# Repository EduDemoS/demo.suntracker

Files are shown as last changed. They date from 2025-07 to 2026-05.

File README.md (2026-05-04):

# EduDemoS Sun-Tracker

This "Sun-Tracker" is our most advanced demonstrator. Similar to a real sunflower, it turns its flower towards the sun to collect as much light as possible. Like the Modular Weather Station, it can send data to the Internet via MQTT. For your convenience there are two sets of instructions. One includes step-by-step instructions for building the complete Sun-Tracker. The other is an abbreviated version suitable for a four-hour workshop and assumes that all soldering and other preparatory work has already been completed.

This repository contains all necessary files and is structured as follows:

- [doc](doc) contains documentation such as
  - assembly manual
  - bill of material
- [code](code) contains program code to run the model
  - [Sun-Tracker preparation firmware](code/Sun-Tracker_Preparation)
  - [Sun-Tracker offline](code/Sun-Tracker)
  - [Sun-Tracker 🌐 IoT ready](code/sun_tracker_iot)
- [dashboards](dashboards) contains example dashboards for ThingsBoard (see [description below](#using-the-example-dashboards)).
- [model](model) contains the printable 3D model

## Using the example dashboards

The example dashboards are tailored for the [IoT variant of the control software](code/sun_tracker_iot/)
To use the example dashboards:

1. Import the JSON file as ThingsBoard dashboard
2. Enter edit mode
3. For each widget adjust:
   - if the target device field is empty: Enter the appropriate target device.
   - if the target device field is not empty, the dashboard features an [entity alias](https://thingsboard.io/docs/user-guide/ui/aliases/#single-entity) to reference the target device. In this case [edit the alias](https://thingsboard.io/docs/user-guide/ui/aliases/#creating-alias) to have it pointing towards the appropriate target device.
4. Save the dashboard

## Licensing

Please note: different licenses apply depending on the type of content.

All documents and 3d models (files ending with .pdf and .stl) are licensed under [CC-BY-NC-SA 4.0](https://creativecommons.org/licenses/by-nc-sa/4.0/).

All files containing code are licensed under [GNU GPL V3](https://www.gnu.org/licenses/gpl-3.0.txt).

## Disclaimer:

Funded by the European Union. Views and opinions expressed are however those of the author(s) only and do not necessarily reflect those of the European Union or the European Education and Culture Executive Agency (EACEA). Neither the European Union nor EACEA can be held responsible for them.

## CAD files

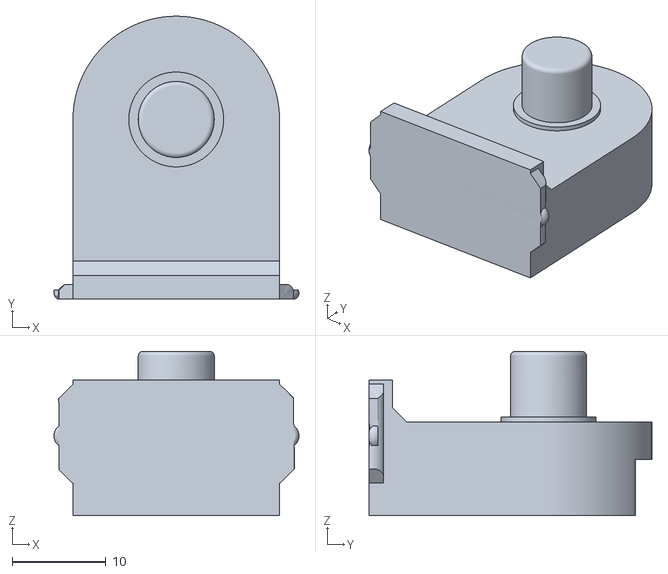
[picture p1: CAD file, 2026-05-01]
model/Flowerhead Joint R.stl
26.1 x 30.1 x 17.5

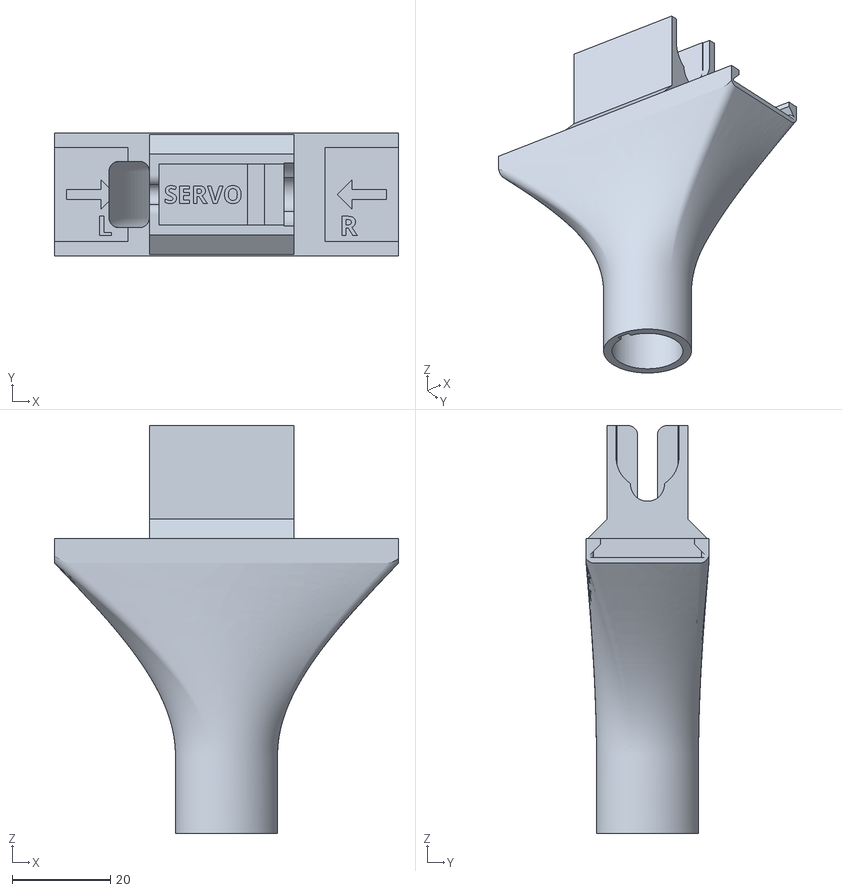
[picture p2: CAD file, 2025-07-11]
model/Stem Top Segment.stl
70.0 x 25.0 x 83.0

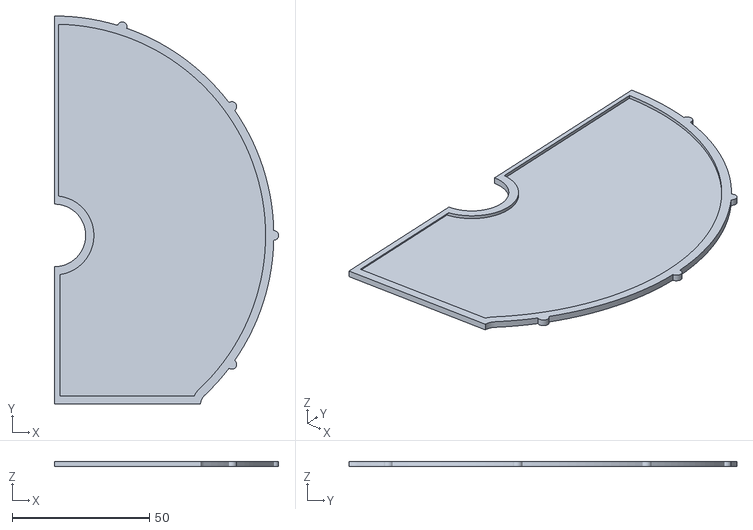
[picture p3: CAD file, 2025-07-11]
model/Pot Cover L.stl
81.7 x 141.5 x 2.00

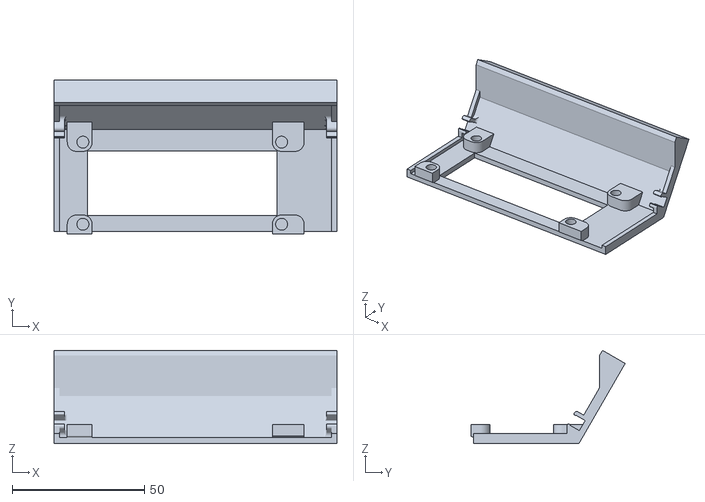
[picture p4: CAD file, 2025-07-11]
model/LCD Frame.stl
106.8 x 58.3 x 35.2

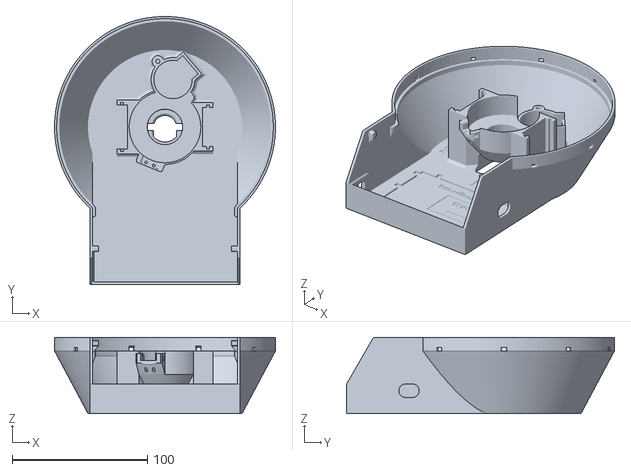
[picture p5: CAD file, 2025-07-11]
model/Flowerpot.stl
163.6 x 198.4 x 56.5

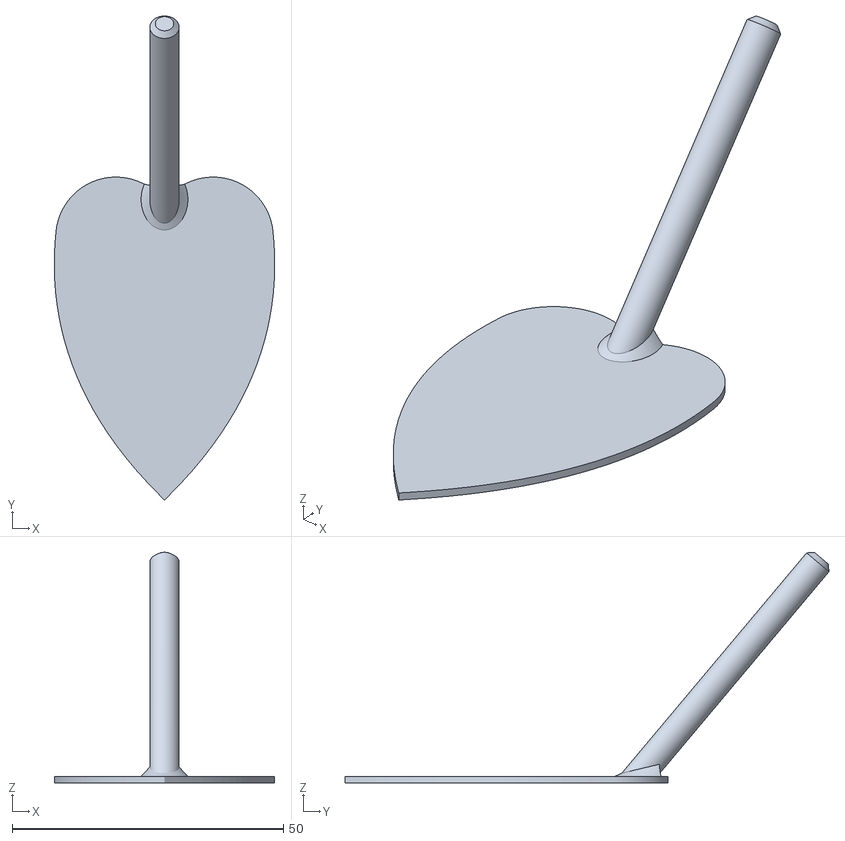
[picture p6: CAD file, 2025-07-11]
model/Stem Leaf.stl
40.6 x 89.3 x 42.5

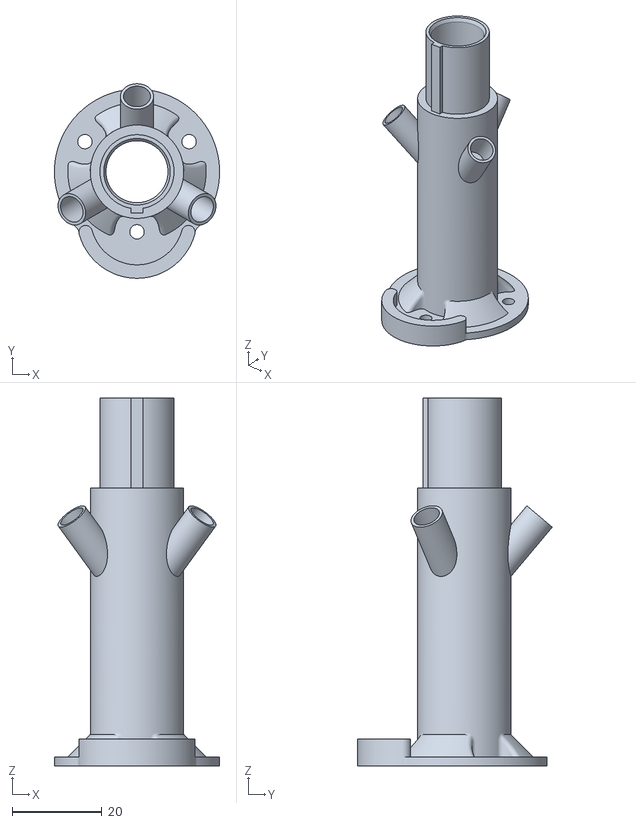
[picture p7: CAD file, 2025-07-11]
model/Stem Leaf Segment.stl
36.8 x 43.4 x 82.0

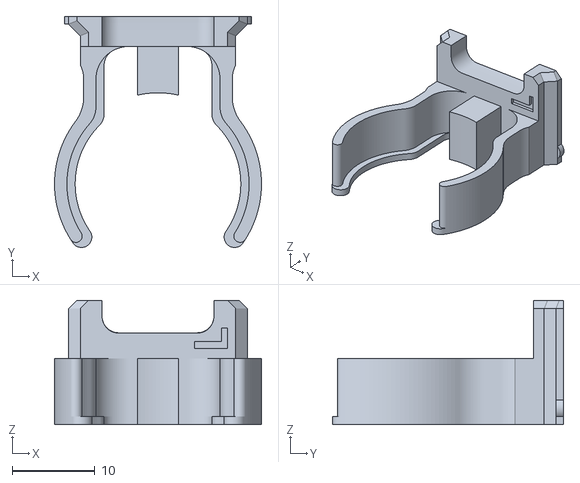
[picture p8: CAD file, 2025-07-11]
model/Flowerhead Clip L.stl
25.0 x 27.9 x 15.0

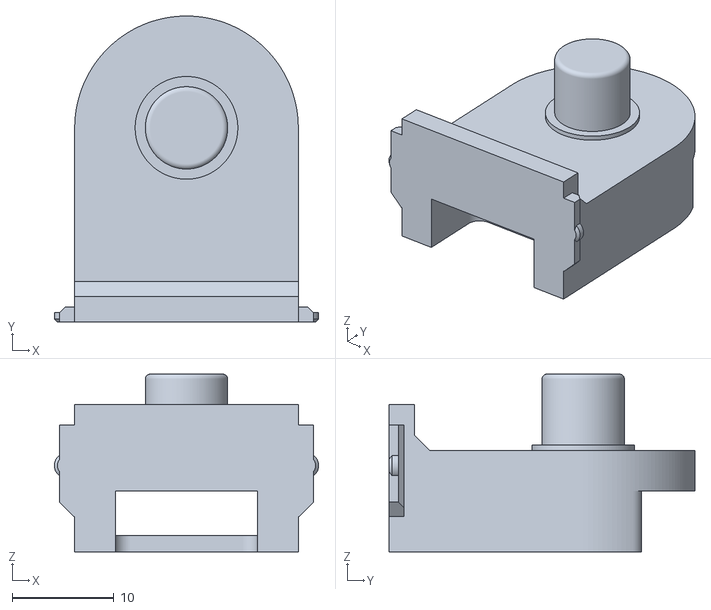
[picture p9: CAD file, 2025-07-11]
model/Flowerhead Joint L.stl
26.0 x 30.1 x 17.5

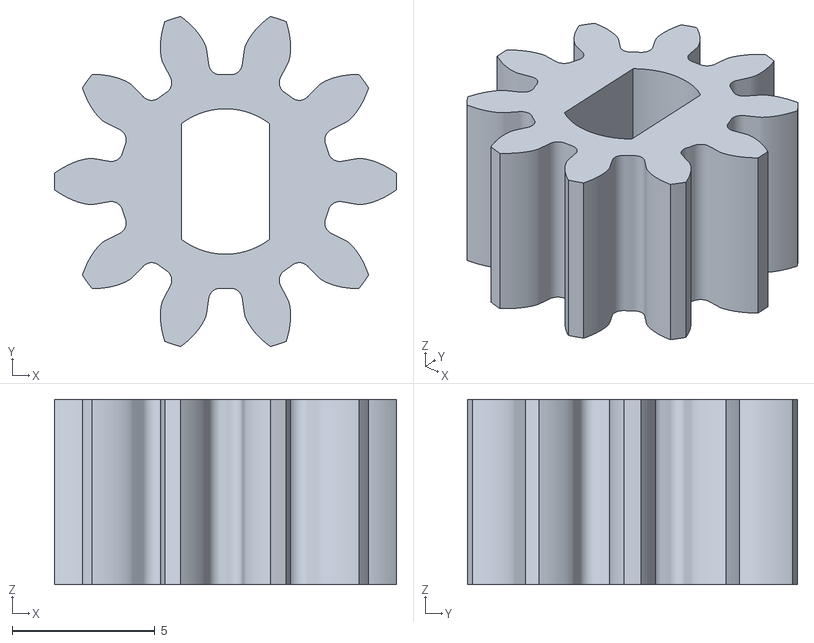
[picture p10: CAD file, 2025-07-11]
model/Motor Gear.stl
12.0 x 11.6 x 6.50

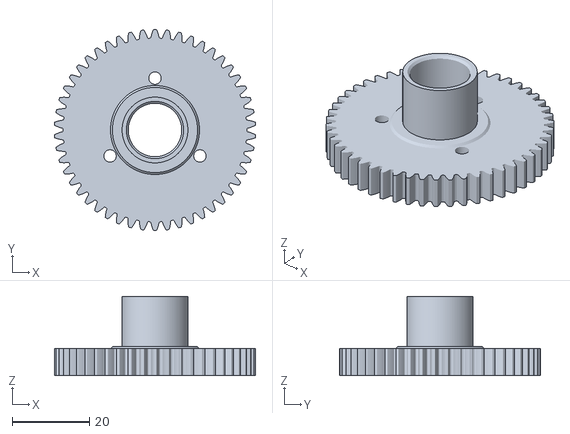
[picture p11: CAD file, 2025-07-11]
model/Large Gear.stl
51.9 x 52.0 x 20.5

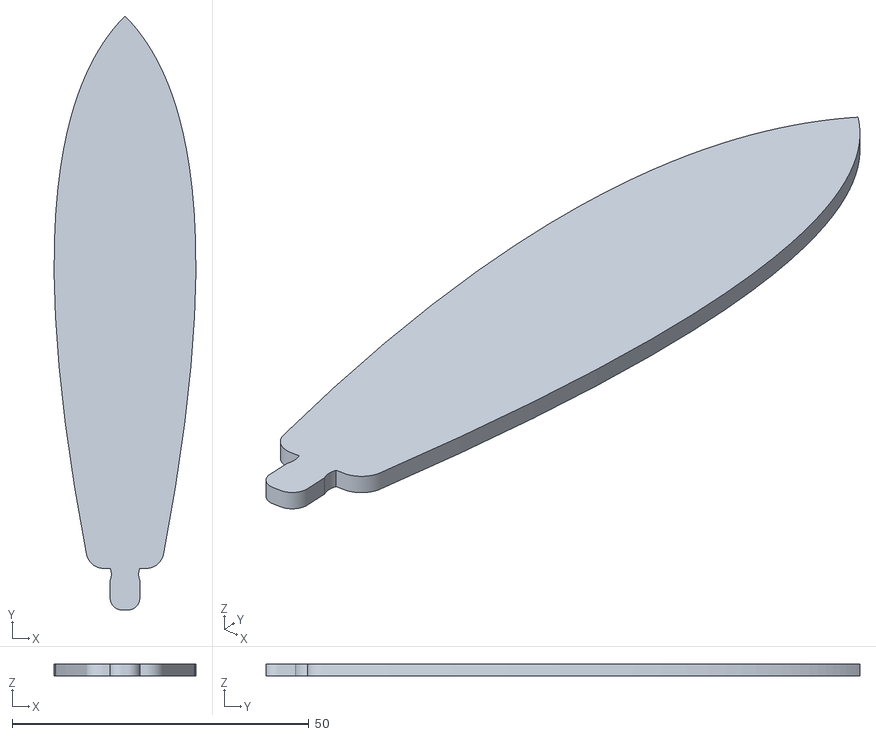
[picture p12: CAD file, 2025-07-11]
model/Flowerhead Leaf.stl
23.9 x 100.0 x 2.00

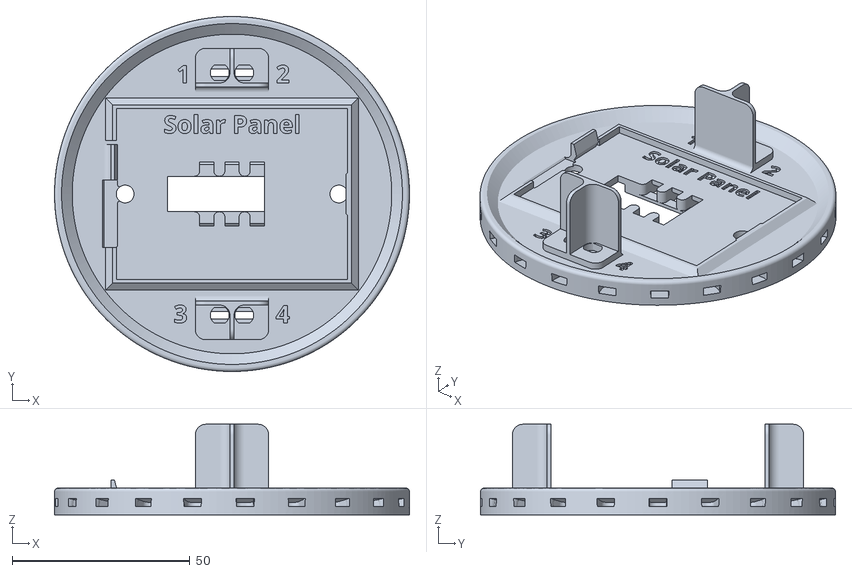
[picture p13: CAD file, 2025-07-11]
model/Flowerhead Base.stl
100.0 x 100.0 x 25.5

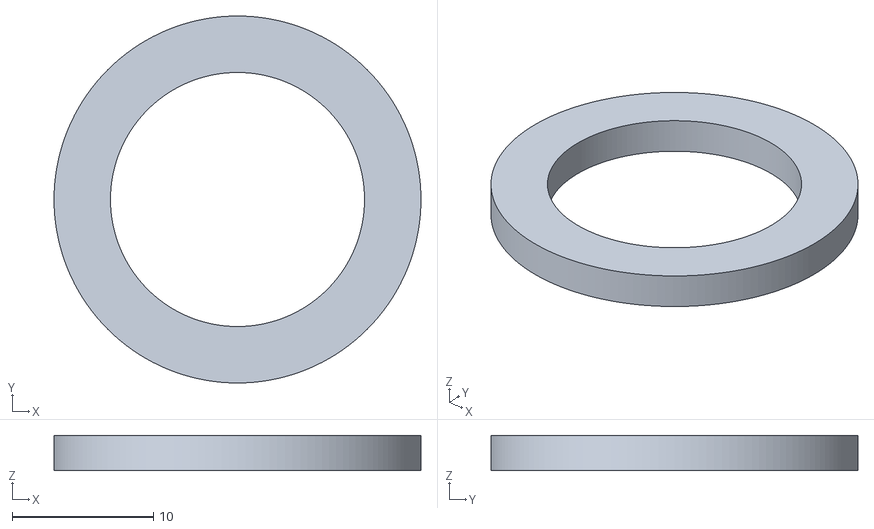
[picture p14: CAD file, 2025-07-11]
model/Bearing Spacer.stl
26.0 x 26.0 x 2.50

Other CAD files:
model/Pot Cover R.stl
model/Stem Segment.stl
model/Flowerhead Clip R.stl

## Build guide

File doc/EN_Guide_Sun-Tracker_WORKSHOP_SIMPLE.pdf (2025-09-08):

# Shortened Workshop Guide Sun-Tracker

# EDUcating through Sustainable DEMOnstrators

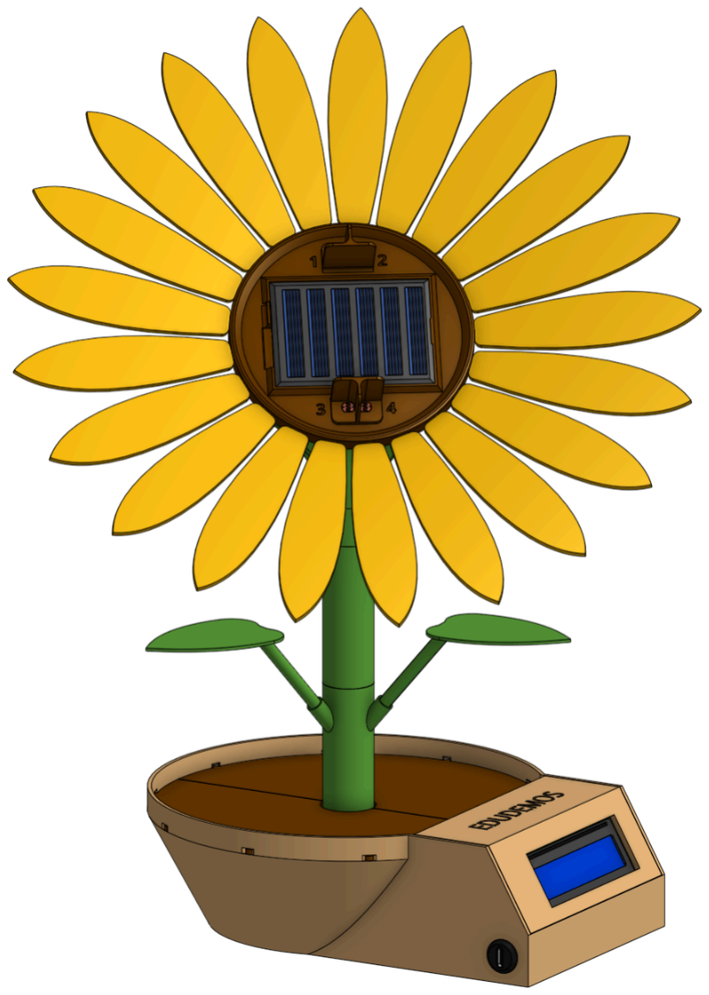
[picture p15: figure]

Funded by the European Union. Views and opinions expressed are however those of the author(s) only and do not necessarily reflect those of the European Union or the European Education and Culture Executive Agency (EACEA). Neither the European Union nor EACEA can be held responsible for them.
V-09.25

# Materials

# Printed Parts

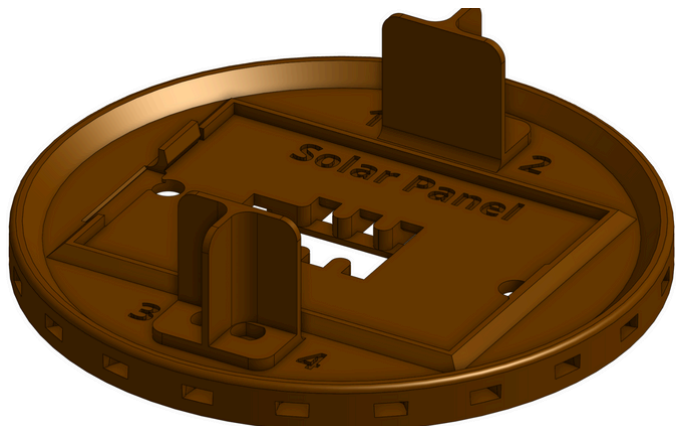
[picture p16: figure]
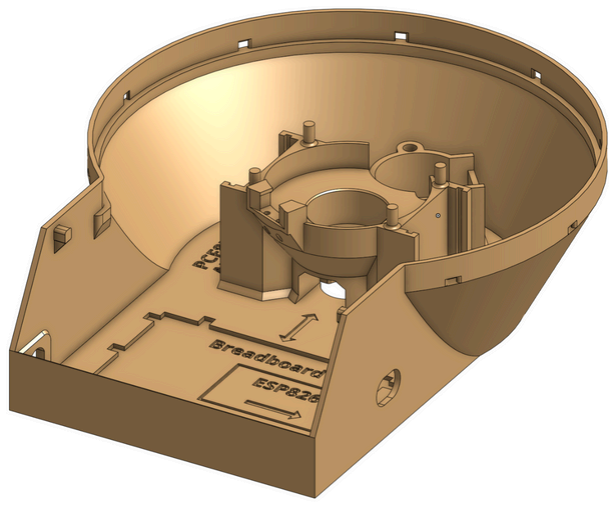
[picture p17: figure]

1x Large Gear | 1x Flowerpot | 1x Motor Gear

1x Stem
Segment

3x Stem Leaf

1x Pot Cover R | 1x Pot Cover L | 1x Stem Top Segment

1x Flowerhead
Clip R

1x Flowerhead
Base

1x Flowerhead
Joint L

1x Flowerhead
Joint R

21x Flowerhead
Leaf

1x Flowerhead
Clip L

1x Leaf
Segment

1x Bearing
Spacer

1x LCD Frame

Print Settings:
All STL-files already have the optimal orientation for printing. Enable supports starting only on the build plate.

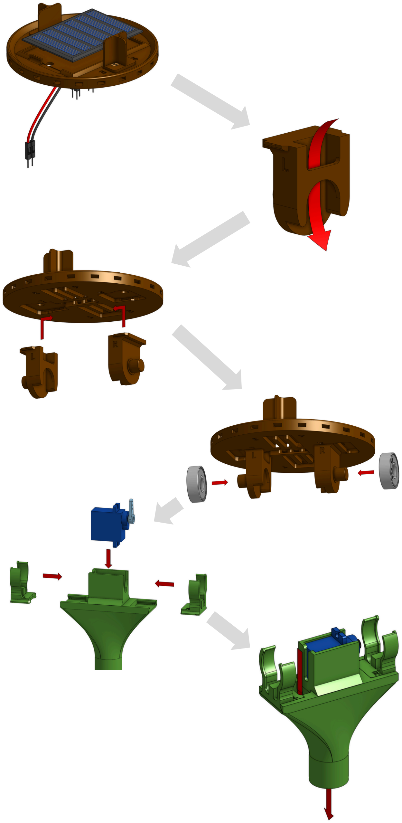
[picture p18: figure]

1.1: Guide the Solar Panel wires from the top through the central hole of the Flowerhead Base and attach it in its frame.

1.2: Then guide all wires (7) coming from the Flowerhead Base through the tunnel in the Flowerhead Joint L.

1.3: Move the Joint L all the way up to the Base and slide it into place.

1.4: Attach Flowerhead Joint R the same way on the opposite side.

1.5: Push the two 608zz Bearings onto the joints.

1.6: Attach both Flowerhead Clips and the Servo Motor in the Stem Top Segment.

1.7: Guide the Servo Motor wires all the way through the hole in the Top Segment.
Do the same with all wires coming from the Flowerhead Assembly.

The wires you have might have different colors than the ones shown here. This is not a problem. Only the connectors are important:
To help you keep track of which wire belongs where, you can note down the actual colors on the “Wire Colors” table.

# 1: Flowerhead Assembly

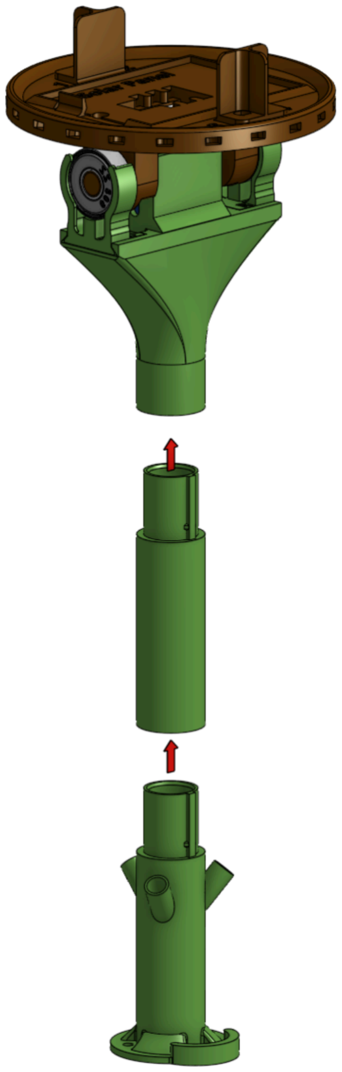
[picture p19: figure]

1.9: Take the Stem Segment, guide the wires through it and attach it to the Top Segment.

1.10: Do the same for the Leaf Segment.

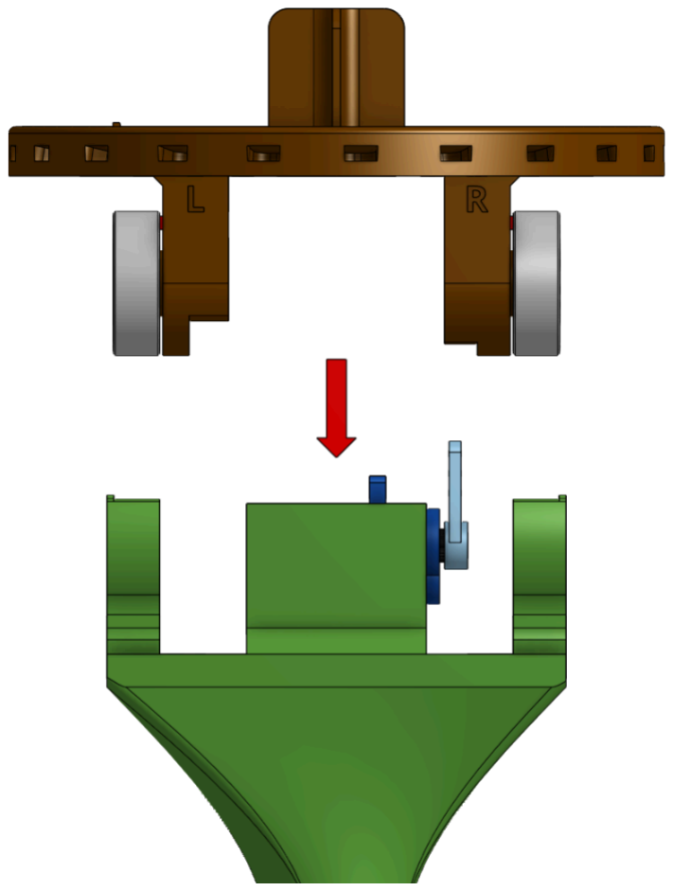
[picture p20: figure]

1.8: Attach the Flowerhead Assembly to the Top Segment by pushing the Bearings into their clips.
Make sure to cleanly pull all the wires through the Top Segment and that they are still grouped together with tape!

# 2: Wiring and Assembly: Flowerpot

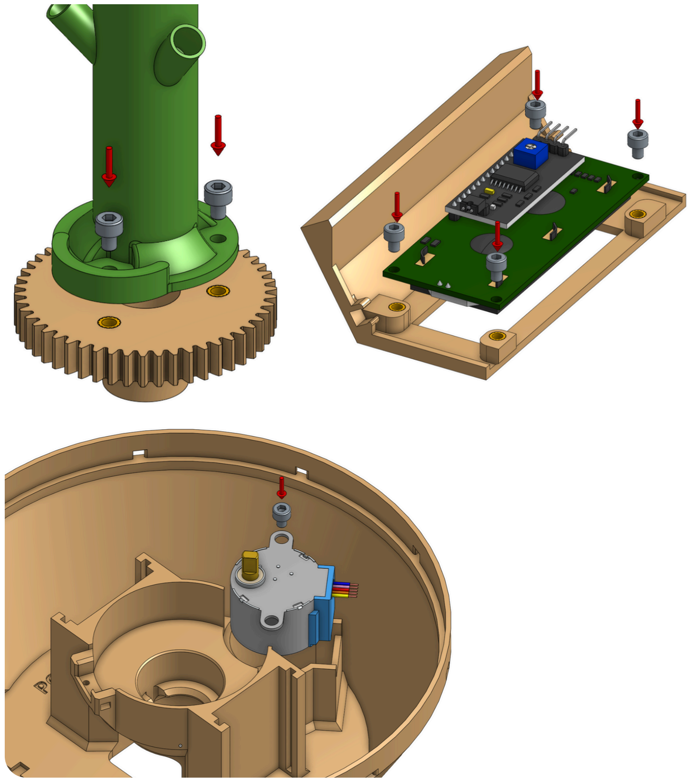
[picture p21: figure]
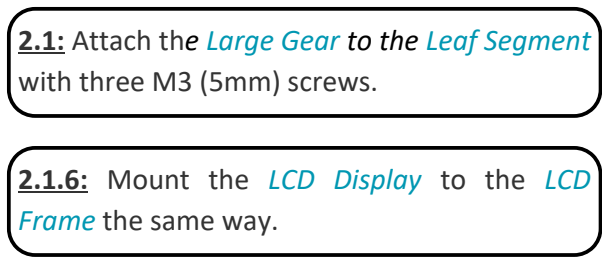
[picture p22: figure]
with three M3 (5mm) screws.; 2.1.6: Mount the LCD Display to the LCD Frame the same way.

2.1: Attach the Large Gear to the Leaf Segment

2.2: Place the Stepper Motor in the Flowerpot. You can mount it with one screw if it’s not tight enough.

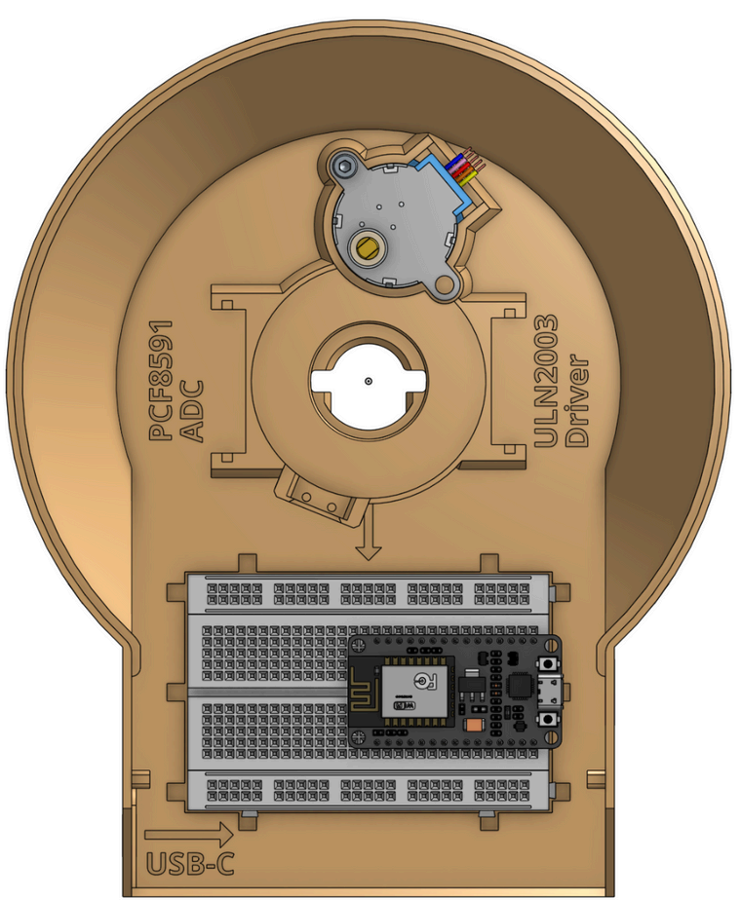
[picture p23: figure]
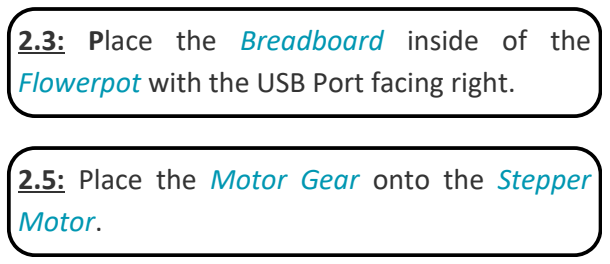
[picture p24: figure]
2.3: Place the Breadboard inside of the; Motor.

Flowerpot with the USB Port facing right.

2.5: Place the Motor Gear onto the Stepper

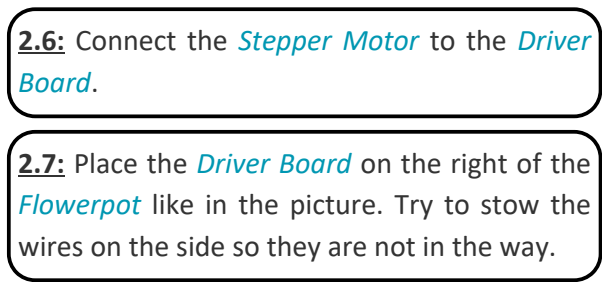
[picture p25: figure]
Board.
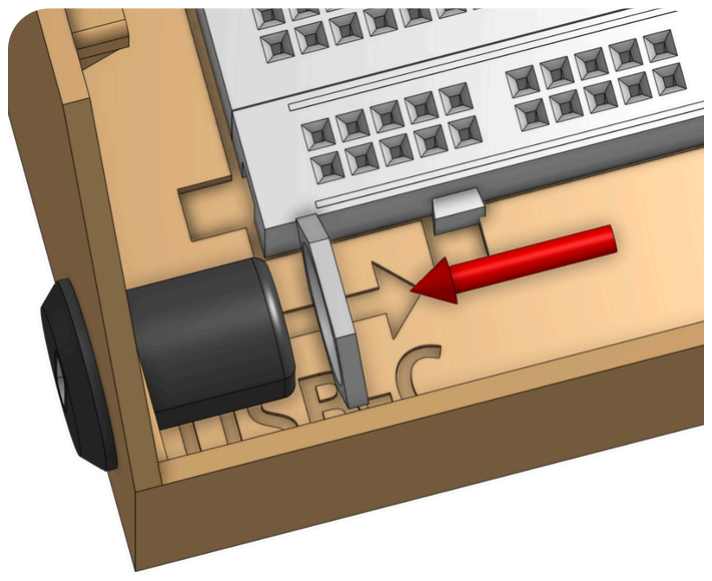
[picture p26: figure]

2.8: Insert the USB-C Connector into its socket and secure it with a nut from the inside.

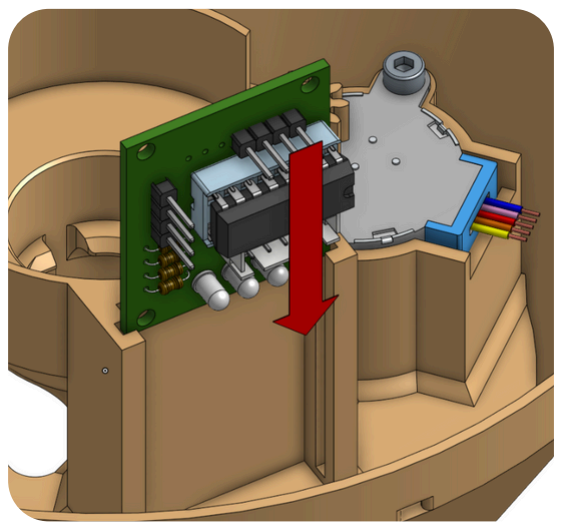
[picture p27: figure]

2.6: Connect the Stepper Motor to the Driver

2.7: Place the Driver Board on the right of the Flowerpot like in the picture. Try to stow the wires on the side so they are not in the way.

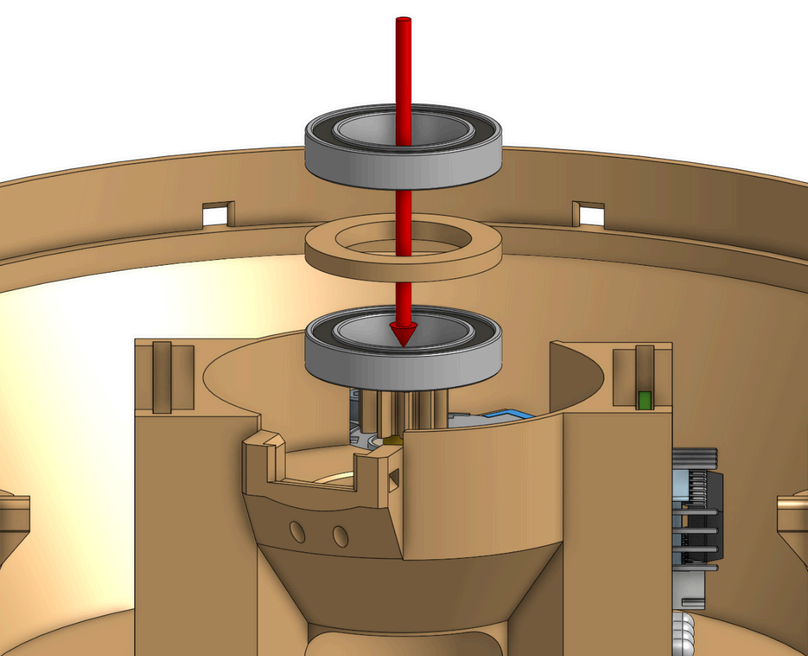
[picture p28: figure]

2.9: Place a Bearing, the Bearing Spacer and then another Bearing in the central socket of the Flowerpot.

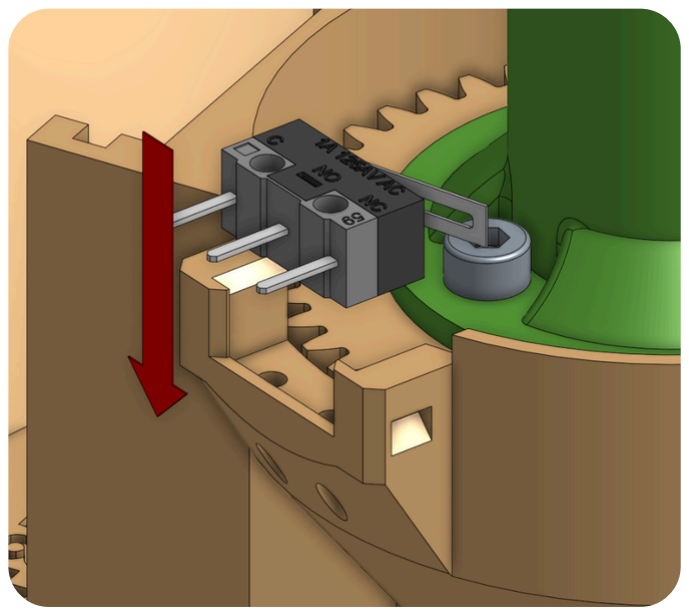
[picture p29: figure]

2.12: Slide the Limit Switch into place with some force.
If the Leaf Segment is in the way you can carefully remove the Motor Gear and rotate it away.

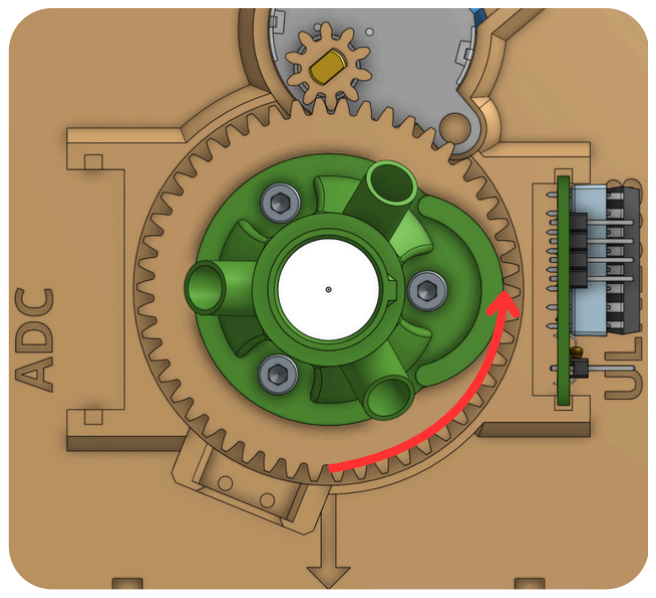
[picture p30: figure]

2.11: Make sure that the little lip of the Leaf Segment roughly points to the right!

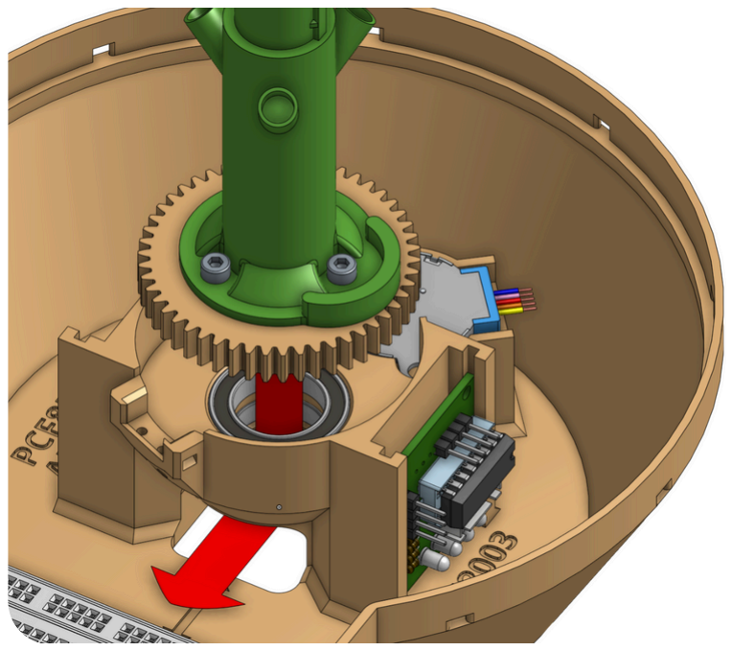
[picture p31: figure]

2.10: Carefully guide the wires through the Bearings and out to the Breadboard. Then slide the Flower Assembly into the Bearings.

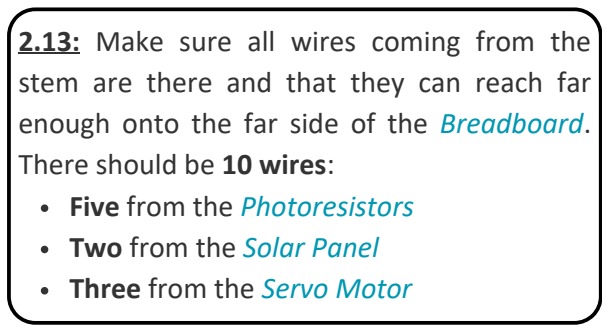
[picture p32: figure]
There should be 10 wires: Five from the Photoresistors Two from the Solar Panel Three from the Servo Motor

2.13: Make sure all wires coming from the stem are there and that they can reach far enough onto the far side of the Breadboard.

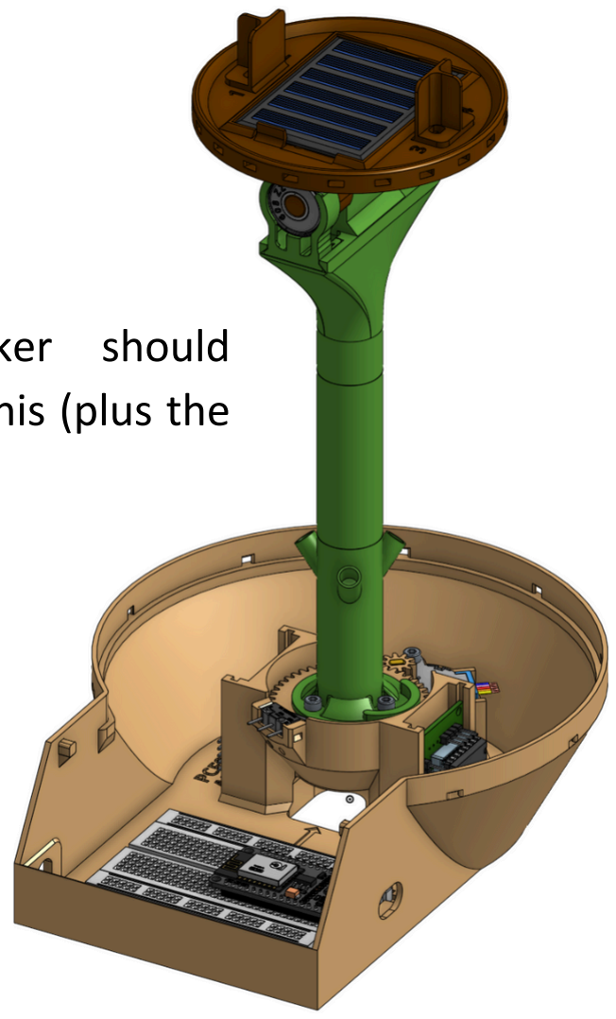
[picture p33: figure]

Your Sun-Tracker should
look similar to this (plus the wires).

# 3: Connecting the remaining electronics

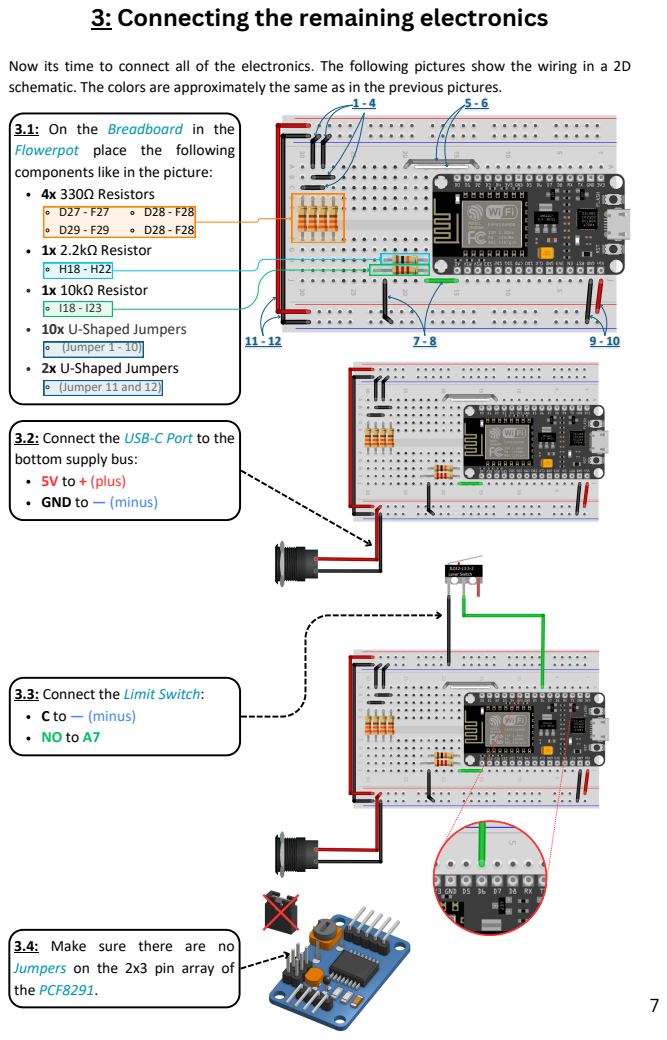
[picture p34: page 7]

Now its time to connect all of the electronics. The following pictures show the wiring in a 2D
schematic. The colors are approximately the same as in the previous pictures.

3.1: On the Breadboard in the
Flowerpot place the following
components like in the picture:
4x 330Ω Resistors
1x 2.2kΩ Resistor
1x 10kΩ Resistor
10x U-Shaped Jumpers
(Jumper 1 - 10)
2x U-Shaped Jumpers
(Jumper 11 and 12)

3.2: Connect the USB-C Port to the
bottom supply bus:
5V to + (plus)
GND to — (minus)

3.3: Connect the Limit Switch:
C to — (minus)

3.4: Make sure there are no
Jumpers on the 2x3 pin array of
the PCF8291.

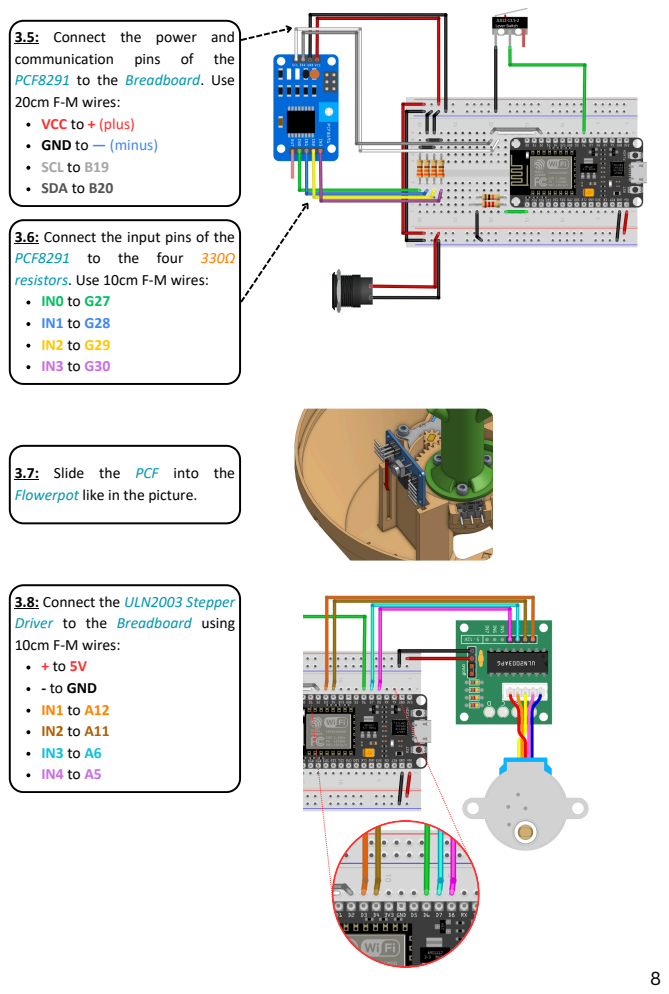
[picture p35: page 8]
communication; pins; the

3.5: Connect the power and
PCF8291 to the Breadboard. Use
20cm F-M wires:
VCC to + (plus)
GND to — (minus)
SCL to B19
SDA to B20

3.6: Connect the input pins of the
PCF8291 to the four 330Ω
resistors. Use 10cm F-M wires:

3.7: Slide the PCF into the
Flowerpot like in the picture.

3.8: Connect the ULN2003 Stepper
Driver to the Breadboard using
10cm F-M wires:
- to GND

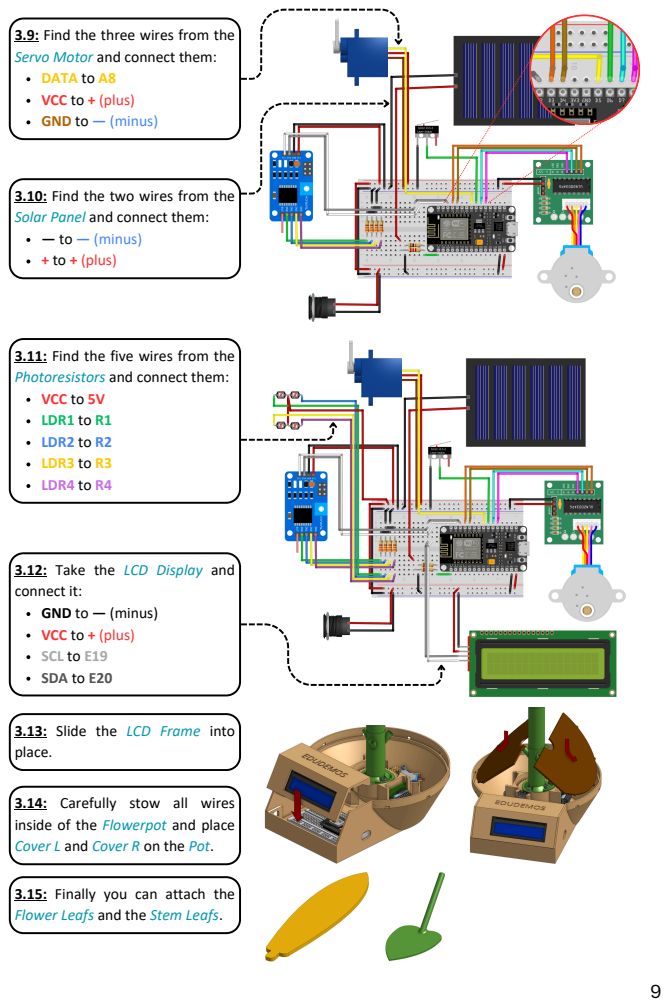
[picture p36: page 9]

3.9: Find the three wires from the
Servo Motor and connect them:
DATA to A8
VCC to + (plus)
GND to — (minus)

3.10: Find the two wires from the
Solar Panel and connect them:
— to — (minus)
+ to + (plus)

3.11: Find the five wires from the
Photoresistors and connect them:
VCC to 5V
LDR1 to R1
LDR2 to R2
LDR3 to R3
LDR4 to R4

3.12: Take the LCD Display and
connect it:
SCL to E19
SDA to E20

3.13: Slide the LCD Frame into
place.

3.14: Carefully stow all wires
inside of the Flowerpot and place
Cover L and Cover R on the Pot.

3.15: Finally you can attach the
Flower Leafs and the Stem Leafs.

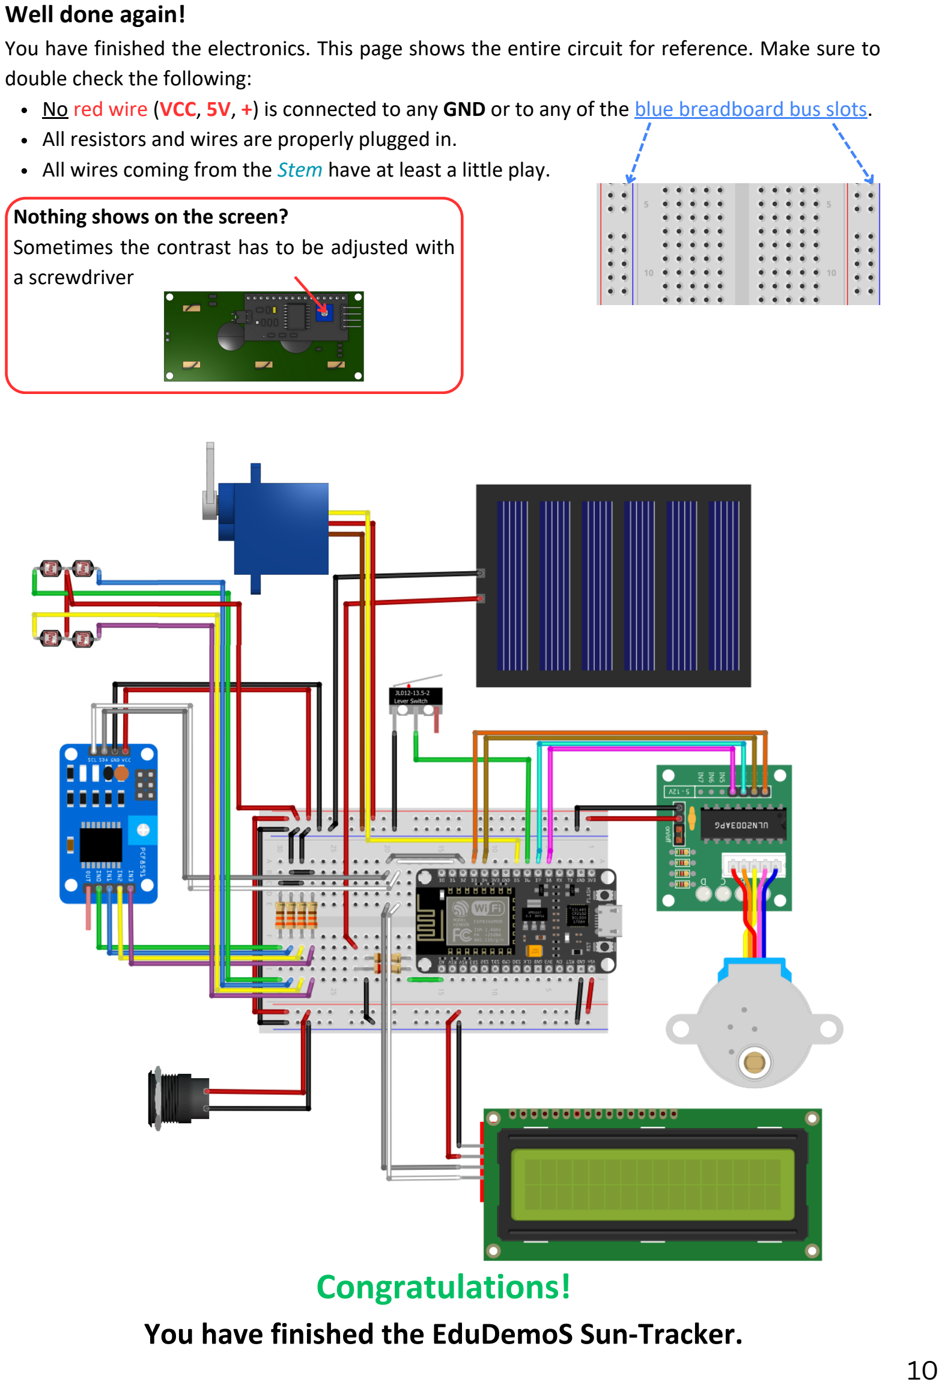
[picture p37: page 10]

Well done again!
You have finished the electronics. This page shows the entire circuit for reference. Make sure to double check the following:
No red wire (VCC, 5V, +) is connected to any GND or to any of the blue breadboard bus slots. All resistors and wires are properly plugged in.
All wires coming from the Stem have at least a little play.

Nothing shows on the screen?
Sometimes the contrast has to be adjusted with
a screwdriver

## Congratulations!

You have finished the EduDemoS Sun-Tracker.

## EduDemoS Sun-Tracker © 2025 by Gerda Stetter Stiftung – Technik macht Spaß! is licensed under Creative Commons Attribution-NonCommercial-ShareAlike 4.0 International. To view a copy of this license, visit https://creativecommons.org/licenses/by-nc-sa/4.0/

## All Circuits were created with Fritzing. (https://fritzing.org/) Some images are based on modules from GrabCAD Library. (https://grabcad.com/library)

# Licensing

# Disclaimer

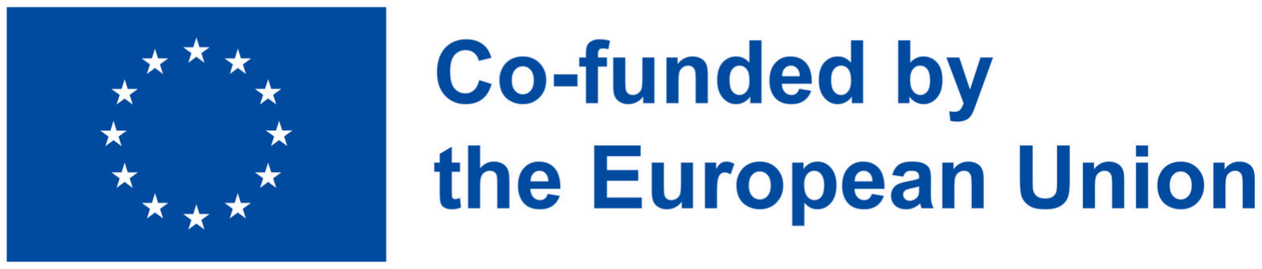
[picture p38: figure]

## Funded by the European Union. Views and opinions expressed are however those of the author(s) only and do not necessarily reflect those of the European Union or the European Education and Culture Executive Agency (EACEA). Neither the European Union nor EACEA can be held

responsible for them.

# Appendix

# Get In Touch With Us

# edudemos@technikmachtspass.org

# EDUcating through Sustainable DEMOnstrators

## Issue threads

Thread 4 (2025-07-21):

Hysteresis for motor movement

uniederer, 2025-07-21:
**Observation**
Especially in lower light conditions, the tracker gets in a state where it keeps running left-right for quite a long time.

**Hypothesis**
This behavior is most probably caused due to noise causing adjustments over and over again.

**Proposal**
Instead (or in addition to) adding a hysteresis to the sensor values, it would make sense to add a hysteresis to target positions as well to avoid such behaviour (i.e. there shall be a minimum distance in reverse direction to be travelled before the motors are moved at all).

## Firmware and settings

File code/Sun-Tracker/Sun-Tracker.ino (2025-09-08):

/*
* This file is part of the EduDemoS Sun-Tracker which is
* co-funded by the European Union.
* Copyright (C) 2025  Gerda Stetter Stiftung - Technik macht Spaß!
*
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

*  +-----------------------------------------------------------------------------------------------------+  *
*                                                                                                           *
*  The algorithm is based on the Arduino Solar Tracker guide:                                               *
*  https://projecthub.arduino.cc/Aboubakr_Elhammoumi/arduino-solar-tracker-77347b                           */


// Include Libraries:
#include "configuration.cpp"
#include <Arduino.h>
#include <Servo.h>
#include <AccelStepper.h>
#include <LiquidCrystal_I2C.h>
#include <ESP8266WiFi.h>
#include <PubSubClient.h>
#include <Wire.h>
#include <EEPROM.h>

//////////////////////////////////////////////////////////////////////////////////////////////////////////////
/////////                                   Objects and Variables                                    /////////

// Define Structure containing Stepper Motor data and create an instance of it:
struct StepperData
{
  int8_t        side = 0;                   // Which side of the Endstop the Stepper is.
  const int16_t stepsPerRotation = 10240;   // Number of Stepper steps in one flower rotation.
  const int16_t stepsPerDegree   = 28;      // Number of Stepper steps in one degree of flower rotation.
  int8_t        inverted         = -1;      // If the Stepper should be inverted.
  bool          zeroPressed      = false;   // If the Endstop Sensor is currently pressed.
};
StepperData stepperData;

#if (!INVERT_STEPPER)
AccelStepper stepper(AccelStepper::FULL4WIRE, PIN_STEPPER_0, PIN_STEPPER_2, PIN_STEPPER_1, PIN_STEPPER_3);
#else
AccelStepper stepper(AccelStepper::FULL4WIRE, PIN_STEPPER_1, PIN_STEPPER_3, PIN_STEPPER_0, PIN_STEPPER_2);
#endif

// Define Structure containing Sensor data:
struct SensorData
{
  bool    tooDark       = false;  // If it's currently too dark.
  int8_t  servoVelocity = 0;      // Actual current Servo speed
  int16_t diffElevation = 0;      // Difference between upper and lower LDR values
  int16_t diffAzimuth   = 0;      // Difference between left and right LDR values
  float   solarVoltage  = 0;      // Voltage generated by the Solar Panel
  uint8_t  PCFReadings[4];        // Raw LDR values received from the PCF Module
};
SensorData sensorData;

// Names for better readability:
#define STEPPER_SIDE_LEFT       1
#define STEPPER_SIDE_RIGHT     -1
#define STEPPER_DIRECTION_CW    1
#define STEPPER_DIRECTION_CCW  -1

// Define second LED Pin:
#ifndef LED_BUILTIN_AUX
#define LED_BUILTIN_AUX 16
#endif

// Create Servo Motor Object:
#define SERVO_PWM_90DEG ((SERVO_PWM_180DEG + SERVO_PWM_0DEG) / 2)
Servo servo;
int16_t servoAngle = SERVO_PWM_90DEG;

// Create LCD Display Object:
LiquidCrystal_I2C lcd(LCD_ADDR, 16, 2);

// Create WiFi and MQTT Objects:
#if ENABLE_WIFI
WiFiClient wifi;
PubSubClient mqtt(wifi);
int wifiStatus = WL_IDLE_STATUS;
bool cancelWiFi = false;
bool cancelMQTT = false;
#endif

// Signature for checking if saved data is valid:
#define EEPROM_SIZE           2
#define EEPROM_ADDR_SIGNATURE 0
#define EEPROM_ADDR_SIDE      1
#define EEPROM_SIGNATURE_BYTE 0x53  // 'S' in hexadecimal


/////////                                    Objects and Variables                                   /////////
//////////////////////////////////////////////////////////////////////////////////////////////////////////////


//////////////////////////////////////////////////////////////////////////////////////////////////////////////
/////////                                    Function Prototypes                                     /////////

// WiFi and MQTT Functions:
bool connectToWiFi();
bool connectToMQTT();
void sendDataToMQTT(float* data, size_t length);

// Functions using the I2C Bus (PCF8591 Module and LCD Display):
int  readPCFChannel(int channelID);
void receiveEvent(int eventCount);
bool scanForDevice(byte address);
inline void checkI2CDevices();
void printToLCD(const char* line1, const char* line2);
void printDataToLCD(int8_t verticalDirection, int8_t horizontalDirection, bool tooDark, float solarVoltage);

// Functions relating to the Stepper and Servo Motors:
void stepperFindZero();
void stepperBacktrack();
void IRAM_ATTR stepperZeroISR();

// Functions relating to saving/reading from flash storage:
bool checkStorageSignature();
bool writeStorageSignature();
bool readStepperSide();
bool writeStepperSide();

// Functions for main functionality:
void determineMovement(SensorData* data);
void moveMotors(SensorData* data);

// Other functions:
template<typename T> T signThresholded(T x);
template<typename T> T sign(T x);
#if ENABLE_STARTUP_CHECKS
bool runDiagnostics(bool checkLCD, bool checkPCF, bool checkWiFi, bool checkMQTT, bool checkServo);
#endif


/////////                                    Function Prototypes                                     /////////
//////////////////////////////////////////////////////////////////////////////////////////////////////////////


//////////////////////////////////////////////////////////////////////////////////////////////////////////////
/////////                                           SETUP                                            /////////
void setup()
{
  // Double the CPU Frequency:
  os_update_cpu_frequency(160);

  // Start communication via USB (Serial):
  Serial.begin(SERIAL_BAUD_RATE);
  while(!Serial) delay(1);

  // Setup LCD Display:
  lcd.begin();

  // Setup I2C communication (LCD and PCF):
  Wire.onReceive(receiveEvent);

  // Print Welcome Message to Serial:
  Serial.println();
  Serial.println("Starting Sun-Tracker......");

  // Print Welcome Message to LCD:
  printToLCD("   Starting     ", 
             "  Sun-Tracker   ");
  delay(3000);

  // Setup Pins:
  pinMode(PIN_STEPPER_0,    OUTPUT);
  pinMode(PIN_STEPPER_1,    OUTPUT);
  pinMode(PIN_STEPPER_2,    OUTPUT);
  pinMode(PIN_STEPPER_3,    OUTPUT);
  pinMode(PIN_SOLAR_ADC,    INPUT);
  pinMode(PIN_ENDSTOP,      INPUT_PULLUP);
  pinMode(LED_BUILTIN_AUX,  OUTPUT);
  digitalWrite(LED_BUILTIN_AUX, HIGH);
  attachInterrupt(PIN_ENDSTOP, stepperZeroISR, FALLING);

  // Connect to WiFi and MQTT:
  #if ENABLE_WIFI
    if(connectToWiFi())
    {
        if(!connectToMQTT())
      {
        cancelMQTT = true;
      }
    }
    else{
      cancelWiFi = true;
    }
  #endif

  // Setup Servo Motor:
  servo.attach(PIN_SERVO_PWM);
  servo.writeMicroseconds(servoAngle);
  
  // Read last known 'side' of Stepper Motor:
  if(!readStepperSide())
  {
    // If Side could neither be read nor written, there must be a storage issue.
    Serial.println("EEPROM Error: Could not read/write Stepper side.");
    
    // Assume that stepper is on the right:
    stepperData.side = STEPPER_SIDE_RIGHT;
  }

  // Setup Stepper Motor:
  stepper.setMaxSpeed(STEPPER_SPEED);
  stepper.setAcceleration(STEPPER_ACCEL);
  stepperFindZero();

  // Run Startup Checks:
  #if ENABLE_STARTUP_CHECKS
    Serial.println("Running Startup Checks...");
    bool result = runDiagnostics(true, true, true, true, true);
    Serial.println(result ? "All good." : "WARNING: Some checks failed!");
  #endif
}
/////////                                           SETUP                                            /////////
//////////////////////////////////////////////////////////////////////////////////////////////////////////////


//////////////////////////////////////////////////////////////////////////////////////////////////////////////
/////////                                            LOOP                                            /////////
void loop()
{ 
  moveMotors(&sensorData);

  // Regularly check for LCD and PCF:
  static long lastI2CScan = 0;
  if((millis() - lastI2CScan) >= 200)
  {
    checkI2CDevices();
    lastI2CScan = millis();
  }

  moveMotors(&sensorData);

  // Regularly read new Sensor values and calculate necessary movement:
  static long lastSensorUpdate = 0;
  if((millis() - lastSensorUpdate) >= SENS_UPDATE_PERIOD)
  {
    determineMovement(&sensorData);
    lastSensorUpdate = millis();
  }

  // Move incrementally every loop (as fast as possible):
  moveMotors(&sensorData);

  // Regularly print to LCD Display:
  static long lastLCDUpdate = 0;
  if((millis() - lastLCDUpdate) >= LCD_UPDATE_PERIOD)
  {
    lastLCDUpdate = millis();
    printDataToLCD(signThresholded(sensorData.diffElevation), 
                   signThresholded(sensorData.diffAzimuth), 
                   sensorData.tooDark, sensorData.solarVoltage);
    
    #if ENABLE_SERIAL_DATA
      for(uint16_t i = 0; i < (sizeof(sensorData.PCFReadings) / sizeof(sensorData.PCFReadings[0])); i++)
      {
        Serial.print(sensorData.PCFReadings[i]);
        Serial.print(",");
      }
      Serial.print(sensorData.solarVoltage);
      Serial.println(",255");
    #endif
  }

  moveMotors(&sensorData);

  // Regularly check wifi/mqtt connection and send data to MQTT Server:
  #if ENABLE_WIFI
  if(!cancelWiFi)
  {
    static long lastMQTTUpdate = 0;
    if((millis() - lastMQTTUpdate) >= MQTT_UPDATE_PERIOD)
    {
      lastMQTTUpdate = millis();

      // Check if WiFi connection is good:
      if(WiFi.status() != WL_CONNECTED)
      {

        connectToWiFi();
        connectToMQTT();
      }

      // Check if MQTT connection is also good:
      if(!mqtt.connected())
      {
        connectToMQTT();
      }

      // Normalize PCF Readings:
      float transmitData[5];
      for(uint8_t i = 0; i < 4; i++)
      {
        transmitData[i] = float(sensorData.PCFReadings[i]);
      }
      transmitData[4] = sensorData.solarVoltage;

      // Send it to the server:
      sendDataToMQTT(transmitData, 5);
    }
  }
  #endif

}
/////////                                            LOOP                                            /////////
//////////////////////////////////////////////////////////////////////////////////////////////////////////////


//////////////////////////////////////////////////////////////////////////////////////////////////////////////
/////////                                         FUNCTIONS                                          /////////

// WiFi and MQTT Functions:

#if ENABLE_WIFI
// Connect to WiFi network.
bool connectToWiFi()
{
  // Return if wifi has been globally canceled:
  if(cancelWiFi || cancelMQTT) return false;

  // Generate pretty SSID char[]:
  char wifi_ssid[]        = WIFI_SSID;
  char wifi_ssid_16[] = "                ";
  for(uint8_t i = 0; i < sizeof(wifi_ssid); i++)
  {
    wifi_ssid_16[i] = wifi_ssid[i];
  }

  Serial.print("Connecting to WiFi network '");
  Serial.print(wifi_ssid);
  Serial.print("' .");
  printToLCD(" Conn. Wifi...  ", wifi_ssid_16);

  // Attempt WiFI connection:
  WiFi.begin(WIFI_SSID, WIFI_PASSWORD);
  uint8_t attempts = 0;
  while((WiFi.status() != WL_CONNECTED) && (attempts < WIFI_MAX_ATTEMPTS))
  {
    attempts++;
    Serial.print(".");
    delay(500);

    // Abort if connection can't be established:
    if(attempts >= WIFI_MAX_ATTEMPTS)
    {
      // Find out error:
      String msg;
    switch(WiFi.status())
    {
      case WL_IDLE_STATUS    : msg = "NOT STARTET YET "; break;
      case WL_NO_SSID_AVAIL  : msg = "NETW. NOT FOUND "; break;
      case WL_CONNECT_FAILED : msg = "FAILED (SIGNAL) "; break;
      case WL_CONNECTION_LOST: msg = "CONNECTION LOST "; break;
      case WL_WRONG_PASSWORD : msg = "INVALID PASSWORD"; break;
      case WL_DISCONNECTED   : msg = "DISCONNECTED    "; break;
      default                : msg = "UNKNOWN ( " + String(WiFi.status()) + ")   "; break;
    }

      Serial.print(" Failed. (");
      Serial.print(msg);
      Serial.println(")");
      printToLCD("  WIFI ERROR:   ", msg.c_str());
      delay(2000);
      return false;
    }
  }

  // If connection was successful:
  Serial.println(" Connected.");
  printToLCD("  Connected.   ", WIFI_SSID);
  return true;
}
#endif

#if ENABLE_WIFI
// Establish connection with the MQTT Broker.
bool connectToMQTT()
{
  // Return if wifi has been globally canceled:
  if(cancelWiFi || cancelMQTT) return false;

  Serial.print("Connecting to MQTT server  '");
  Serial.print(MQTT_SERVER);
  Serial.print("' .");
  printToLCD(" Conn. MQTT...  ", MQTT_SERVER);

  // Set MQTT Server:
  mqtt.setServer(MQTT_SERVER, MQTT_PORT);

  // Check if WiFi is connected:
  if(WiFi.status() != WL_CONNECTED)
  {
    Serial.println("Failed. No WiFi.");
    printToLCD("  MQTT ERROR:   ", 
               "    No WiFi     ");
    delay(2000);
    return false;
  }

  // Attempt MQTT connection:
  uint8_t attempts = 0;
  while(!mqtt.connected() && (attempts < MQTT_MAX_ATTEMPTS))
  {
    attempts++;
    Serial.print(".");

    // Attempt connection:
    if(mqtt.connect(MQTT_CLIENT_ID, MQTT_USERNAME, MQTT_PASSWORD))
    {
      Serial.println("Connected.");
      printToLCD("  Connected.   ", MQTT_SERVER);
      delay(2000);
      return true;
    }
  }

  // If connection has failed:
  // Determine error message:
  String errorMsg;
  switch(mqtt.state())
  {
    case -4:  errorMsg = "CONN. TIMEOUT   "; break;
    case -3:  errorMsg = "CONN. LOST      "; break;
    case -2:  errorMsg = "CONN. FAILED    "; break;
    case -1:  errorMsg = "DISCONNECTED    "; break;
    case  1:  errorMsg = "BAD PROTOCOL    "; break;
    case  2:  errorMsg = "BAD CLIENT ID   "; break;
    case  3:  errorMsg = "UNAVAILABLE     "; break;
    case  4:  errorMsg = "BAD CREDENTIALS "; break;
    case  5:  errorMsg = "UNAUTHARIZED    "; break;
    default:  errorMsg = "UNKNOWN         "; break;
  }


  Serial.print("Failed (");
  Serial.print(errorMsg);
  Serial.println(").");
  printToLCD("  MQTT ERROR:   ", errorMsg.c_str());
  delay(1000);
  return false;
}
#endif

#if ENABLE_WIFI
// Send Photoresistor values and Solar Panel voltage to the MQTT Broker / thingspeak.
void sendDataToMQTT(float* data, size_t length)
{
  String topic = "channels/" + String(MQTT_CHANNEL_ID) + "/publish";
  String message = "";

  for(uint i = 0; i < length; i++)
  {
    message += "&field" + String(i+1) + "=" + String(data[i], 2);
  }
  message.remove(0, 1);   // Remove first '&'

  mqtt.publish(topic.c_str(), message.c_str());
}
#endif

// Functions using the I2C Bus (PCF8591 Module and LCD Display):

// Read the ADC value from a given channel on the PCF8591 module.
int  readPCFChannel(int channelID)
{
  Wire.beginTransmission(PCF8591_ADDR);
  Wire.write(0x40 | channelID);
  byte errorPCF = Wire.endTransmission();

  // Check for PCF errors:
  if(errorPCF)
  {
    // Evaluate Error code:
    Serial.print("I2C Error: ");
    Serial.print(errorPCF);
    Serial.print(" - ");
    switch(errorPCF)
    {
      case 1:  Serial.println("Data too long for buffer."); break;
      case 2:  Serial.println("NACK on address transmission (Device not found)"); break;
      case 3:  Serial.println("NACK on data transmission."); break;
      case 4:  Serial.println("Unknown I2C failure."); break;
      default: Serial.println("Unknown I2C failure."); break;
    }

    // Check for LCD Display:
    if(!scanForDevice(LCD_ADDR))
    {
      Serial.print("       --> LCD Display not detected! Check wiring. Check I2C address in datasheet (0x");
      Serial.print(LCD_ADDR, HEX);
      Serial.println("). If this happens sporadically, power off, wait 15s, power on.");
    }
    else
    {
      Serial.println("       --> LCD Display is connected.");
    }

    // Check for PCF Module:
    if(!scanForDevice(PCF8591_ADDR))
    {
      Serial.print("       --> PCF8591     not detected! Check wiring. Check I2C address in datasheet(0x");
      Serial.print(PCF8591_ADDR, HEX);
      Serial.println("). If this happens sporadically, power off, wait 15s, power on.");
    }
    else
    {
      Serial.println("       --> PCF8591     is connected.");
    }
    
    delay(100);
    return 0;
  }

  //Return voltage value:
  Wire.requestFrom(PCF8591_ADDR, 2);
  if(Wire.available() >= 2)
  {
    Wire.read();
    return Wire.read();
  }
  else
  {
    // PCF is not responding (despite no error before, this should not happen):
    Serial.println("I2C Error: PCF8591 is not responding with data!");
    delay(100);
  }
  return 0;
}

// Callback function for the I2C bus.
void receiveEvent(int eventCount)
{
  while(0 < Wire.available()) char c = Wire.read();
}

// Check if a device with the given address is on the I2C bus.
bool scanForDevice(byte address)
{
  Wire.beginTransmission(address);
  return (Wire.endTransmission() == 0); // Returns true if device is found.
}

// Check if LCD Display and PCF Module are properly connected. Run this function regularly.
inline void checkI2CDevices()
{
  // Check both devices:
  bool errorPCF = !scanForDevice(PCF8591_ADDR);
  bool errorLCD = !scanForDevice(LCD_ADDR);

  static bool ledStateAUX = false;

  // Blink LED in case of LCD/LED error:
#ifdef LED_BUILTIN_AUX
  if(errorPCF || errorLCD)
  {
    // Determine blink intervall:
    uint16_t blinkIntervall;
    if(errorLCD) blinkIntervall = 500;     // ... if only LCD is not found
    else         blinkIntervall = 1000;    // ... as soon as PCF is not found

    // Blink LED:
    static long lastBlinkupdate = 0;
    if((millis() - lastBlinkupdate) >= blinkIntervall)
    {
      digitalWrite(LED_BUILTIN_AUX, ledStateAUX ? LOW : HIGH);
      ledStateAUX = !ledStateAUX;
      lastBlinkupdate = millis();
    }
  }
  else
  {
    // If both modules are connected, turn off LED:
    digitalWrite(LED_BUILTIN_AUX, HIGH);
    ledStateAUX = false;
  }
  #endif

  // In case of only PCF error, print it to LCD:
    if(errorPCF && !errorLCD && !ledStateAUX)
    {
      printToLCD("   PCF Module   ",
                 "   NOT FOUND!   ");
    }
}

// Print both lines to the LCD Display. line1 and line2 must have 16 characters.
// Only actually updates the screen if the symbol has changed.
void printToLCD(const char* line1, const char* line2)
{
  // Remember last lines:
  static char lastLine1[17] = "                ";
  static char lastLine2[17] = "                ";

  for(uint8_t i = 0; i < 16; i++)
  {
    char c1 = (line1[i] == '\0') ? ' ' : line1[i];  // Replace null with space
    char c2 = (line2[i] == '\0') ? ' ' : line2[i];

    // Update character in the first line:
    if(c1 != lastLine1[i])
    {
      lcd.setCursor(i, 0);
      lcd.print(c1);
      lastLine1[i] = c1;
    }

    // Update character in the second line:
    if(c2 != lastLine2[i])
    {
      lcd.setCursor(i, 1);
      lcd.print(c2);
      lastLine2[i] = c2;
    }
  }
}

// Print an indicator of the current movement direction, the Motor angles and the current
// Solar Panel Voltage to the LCD Display.
void printDataToLCD(int8_t verticalDirection, int8_t horizontalDirection, bool tooDark, float solarVoltage)
{
  char line1[3] = "  ";
  char line2[3] = "  ";

  // Invert values:
  verticalDirection   *= -1;
  horizontalDirection *= -1;

  if(tooDark)
  {
    strcpy(line1, "--");
    strcpy(line2, "--");
  }
  else
  {
    // Determine horizontal component:
    if(horizontalDirection > 0)
    { // Left
      line1[0] = '#';
      line2[0] = '#';
    }
    else if(horizontalDirection < 0)
    { // Right
      line1[1] = '#';
      line2[1] = '#';
    }

    // Determine vertical component:
    if(verticalDirection > 0)
    { // Up
      line1[0] = '#';
      line1[1] = '#';
    }
    else if(verticalDirection < 0)
    {
      line2[0] = '#';
      line2[1] = '#';
    }
  }

  // If brightest spot has been found:
  if(!tooDark && !verticalDirection && !horizontalDirection)
  {
    strcpy(line1, "##");
    strcpy(line2, "##");
  }

  // +----------------+
  // |## Volt SRV STP |
  // |## 2.1V 120  34 |
  // +----------------+

  // Calculate Stepper angle:
  int16_t stepperAngle = stepper.currentPosition() / stepperData.stepsPerDegree;

  // Generate LCD Content:
  char lcdLine1[17];
  char lcdLine2[17];
  snprintf(lcdLine1, sizeof(lcdLine1), "%s Volt SVO STP",  line1);
  snprintf(lcdLine2, sizeof(lcdLine2), "%s %.1fV %3d %3d", line2, solarVoltage, servo.read(), stepperAngle);

  printToLCD(lcdLine1, lcdLine2);
}

// Functions relating to the Stepper Motor:
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

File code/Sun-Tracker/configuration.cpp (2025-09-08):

/*
* This file is part of the EduDemoS Sun-Tracker which is
* co-funded by the European Union.
* Copyright (C) 2025  Gerda Stetter Stiftung - Technik macht Spaß!
*
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

*  +-----------------------------------------------------------------------------------------------------+  *
*                                                                                                           *
*  This file lets you change certain parameters of the Sun-Tracker and adapt its behaviour.                 */


// Toggle features:
#define ENABLE_WIFI           0 // [0, 1]   If WiFi/MQTT should be used (MQTT data below has to be correct).
#define ENABLE_SERIAL_DATA    1 // [0, 1]   If LDR/solar values should be sent via serial.
#define ENABLE_STARTUP_CHECKS 0 // [0, 1]   If hardware/connection checks should be made on startup.

// Sunflower behaviour:
#define LCD_UPDATE_PERIOD   50  // [ms]     Time to wait between updating the LCD display.
#define SENS_UPDATE_PERIOD  50  // [ms]     Time to wait between reading/evaluating sensors.
#define MIN_BRIGHTNESS      1   // [1, 255] Minimum necessary brightness to start moving.
#define DIFF_BRIGHTNESS     1   // [1, 255] Minimum necessary brightness difference
                                //          between neighbouring LDRs to start moving.
#define BACKTRACK_LIMIT     100 // [deg]    How far the Flower can turn before reversing
                                //          to prevent tangling wires. Must be > 95deg

#define INVERT_STEPPER      0     // [0,1]     Fully invert the turning-direction of the Stepper Motor
#define STEPPER_SPEED       700   // [0, 1000] Max. speed of the Stepper Motor
#define STEPPER_ACCEL       1000  // [0, 1000] Max. acceleration of the Stepper Motor

// WiFi Settings:
#define WIFI_SSID           "YOUR_WIFI_NAME"      //  Name of your WiFi network
#define WIFI_PASSWORD       "YOUR_WIFI_PASSWORD"  //  Password of your WiFi network
#define WIFI_MAX_ATTEMPTS   20                    //  How many times to attempt to connect
                                                  //  before resuming without WiFi

// MQTT Settings:
#define MQTT_PORT               1883                        // MQTT Broker Port
#define MQTT_SERVER             "mqtt3.thingspeak.com"      // MQTT Broker Address
#define MQTT_CHANNEL_ID         1234567                     // Thingspeak channel ID
#define MQTT_USERNAME           "YOUR_MQTT_USERNAME"        // MQTT Username
#define MQTT_CLIENT_ID          "YOUR_THINGSPEAK_ID"        // Thingspeak Client ID (identical to username)
#define MQTT_PASSWORD           "YOUR_MQTT_PASSWORD"        // MQTT Password
#define MQTT_UPDATE_PERIOD      2000                        // [ms] Time to wait before sending data to MQTT
#define MQTT_MAX_ATTEMPTS       10

// Serial Settings:
#define SERIAL_BAUD_RATE    9600    // [bits/s] // Communication speed for USB Connection

// I2C Settings:
#define PCF8591_ADDR        0x48    // I2C Address of the PCF8591 Module
#define LCD_ADDR            0x27    // I2C Address of the LCD Display

// Pins:
#define PIN_ENDSTOP         12      // GPIO Pins for all connections. The numbers are different from the ones
#define PIN_SOLAR_ADC       A0      // printed on the board! Check the Pinout Diagram for the correct numbers
#define PIN_SERVO_PWM       14      // if you want to make changes:
#define PIN_STEPPER_0       2       // https://www.az-delivery.de/en/products/nodemcu
#define PIN_STEPPER_1       0
#define PIN_STEPPER_2       15
#define PIN_STEPPER_3       13

// Resistors:
#define RESISTOR_SOL1       2.2     // Resistor 1 of the Solar Panel voltage divider
#define RESISTOR_SOL2       10.0    // REsistor 2 of the Solar Panel voltage divider

// Fine control Servo Motor angle:
#define SERVO_PWM_180DEG 2000   // Increase to ~2300 if Servo doesn't fully turn
#define SERVO_PWM_0DEG   1000   // Decrease to ~ 700 if Servo doesn't fully turn

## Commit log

2025-07-11 Mirror original data from 21.04.2025
    [Bearing Spacer.stl, Flowerhead Base.stl, Flowerhead Clip L.stl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]
2026-04-28 Extend the lever cutout to fix #6
    [Flowerhead Joint R.stl]

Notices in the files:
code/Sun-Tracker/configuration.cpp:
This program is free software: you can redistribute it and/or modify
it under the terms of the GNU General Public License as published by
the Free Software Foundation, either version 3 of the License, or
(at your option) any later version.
